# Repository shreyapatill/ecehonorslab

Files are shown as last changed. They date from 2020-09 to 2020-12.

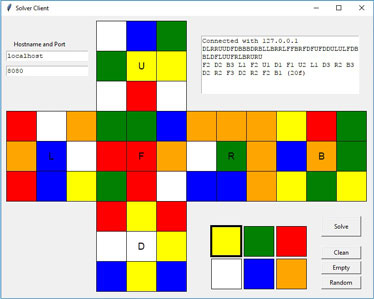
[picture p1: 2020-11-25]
RubiksSolver/gui_client.jpg

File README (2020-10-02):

By: Alex Zhang, Shreya Patil, Aryan Gupta
Project Proposal Guideline
Introduction

Statement of Purpose
The goal of our project is to construct and program a machine that can autonomously solve a Rubik’s Cube puzzle, starting from any random combination. 

Background Research

We are working on this project because we thought it would be cool to create something that could solve the complicated puzzle that is the Rubik’s Cube. We looked into what people have used to build a Rubik’s cube solver and modified their designs to build our project.
This project is similar to the Rubik’s Cube Solver back in Spring 2020. However, we plan to make the mechanical frame out of legos or 3d printing to cut down on cost and need for mechanical design experience. We also plan to use two cameras to scan the faces of the cube. 

System Overview

Rubik’s Cube: Would be a shame if this were missing...
UI: Where a human can input the colors of the faces. This is the input of the machine.
Each color has a number, you run a python code that allows you to type in the numbers that represent the cube
Data is sent to the Raspberry Pi by USB wire
IR Sensor: Senses whether the cube is in position and ready to be solved
Raspberry Pi: The brains. Figures out the status of the cube, calculates the solution, and sends the moves to the motors
Motor Drivers: The interface between the motor and the Pi
Stepper Motors: Rotates the faces of the cube to solve it

Parts

Rubik’s Cube
Rubik's Cube on Amazon
$6
Raspberry Pi 3 B+
ECE Supply Center - 740162520
$42
Raspberry Pi Power Supply
ECE Supply Center - 740162522
$11
MicroSD Card
MicroSD Card on Amazon 
$6
Six Stepper Motors
Stepper Motor
6 * 6 = $36 total
Holding torque: 0.26Nm (need 0.05Nm for speedcubes)
Set of Three Motor Drivers
Set of Three Motor Drivers on Amazon
$30
Mechanical Frame (3d printed or legos)
IR Sensors
IR Sensor on Amazon 
$9
TOTAL: $140 + legos (if we plan to go with those)
 
Possible Challenges

Frame design &  material (lego or 3-D printing?)
Creating a UI to input faces
Virtual communications/construction
Code it so the solver stops at the solution
 
References

	[1]J. Flatland and P. Rose, "jayflatland/HighFrequencyTwister", GitHub, 2020. [Online]. Available: https://github.com/jayflatland/HighFrequencyTwister/blob/master/LICENSE. [Accessed: 18- Sep- 2020].
	[2]"Adafruit's Raspberry Pi Lesson 10. Stepper Motors", Adafruit Learning System, 2020. [Online]. Available: https://learn.adafruit.com/adafruits-raspberry-pi-lesson-10-stepper-motors. [Accessed: 18- Sep- 2020].
	[3]N. Knopf and J. Swiezy, Web.mit.edu, 2020. [Online]. Available: http://web.mit.edu/6.111/www/f2017/projects/knopf_Project_Design_Presentation.pdf. [Accessed: 18- Sep- 2020].
	[4]"rubix cube transparent - Google Search", Google.com, 2020. [Online]. Available: https://www.google.com/search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. [Accessed: 18- Sep- 2020].
	[5]SenorJuan, “Torque on Conventional Cubes,” SpeedSolving Puzzles Community, 27-Jan-2020. [Online]. Available: https://www.speedsolving.com/threads/torque-on-conventional-cubes.76309/. [Accessed: 20-Sep-2020]. 
	[6]"MineLT/CubeSolver", GitHub, 2020. [Online]. Available: https://github.com/MineLT/CubeSolver. [Accessed: 27- Sep- 2020].

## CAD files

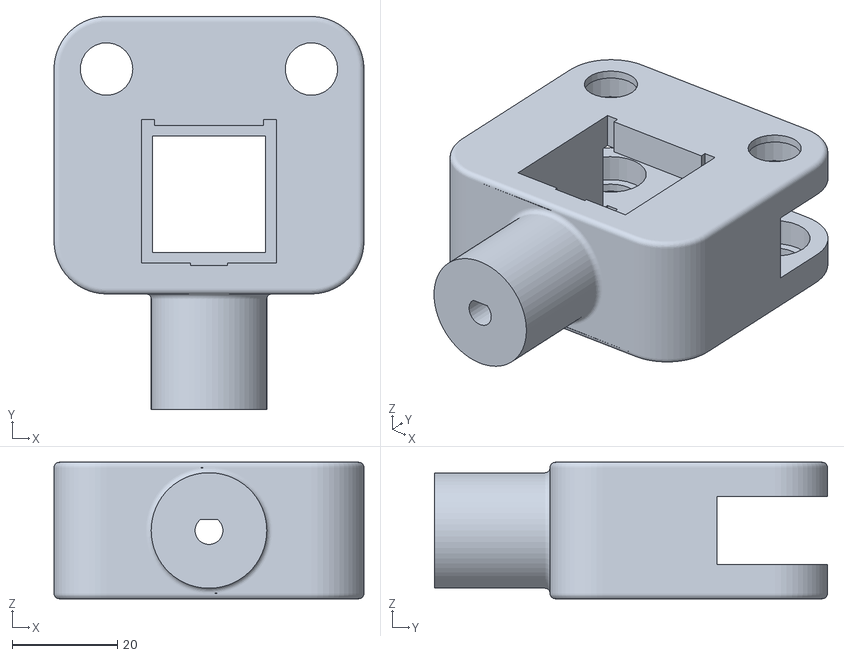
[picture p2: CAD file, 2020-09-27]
3d Models/Phase 5 Claw/Claw5 - Main Body.stl
59.0 x 74.8 x 26.0

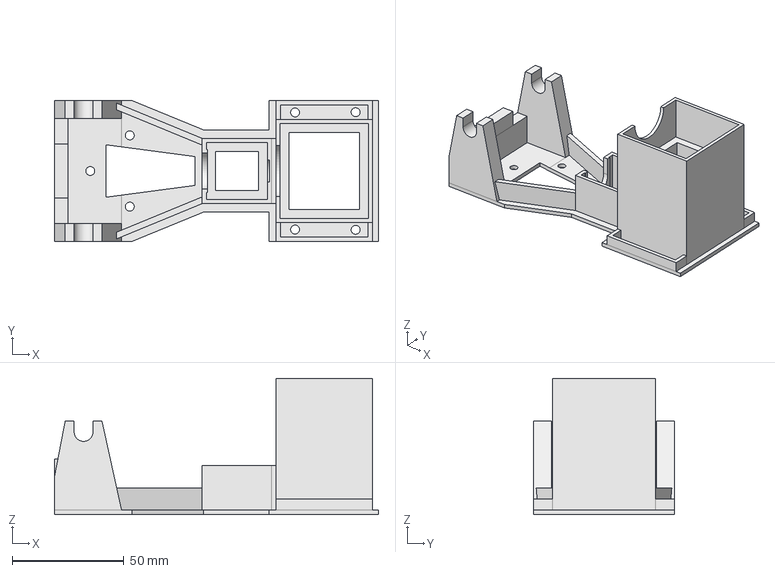
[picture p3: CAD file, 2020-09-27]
3d Models/Phase 2 Speedster/Assembly Tray.FCStd
144.9 x 63.0 x 61.0 mm

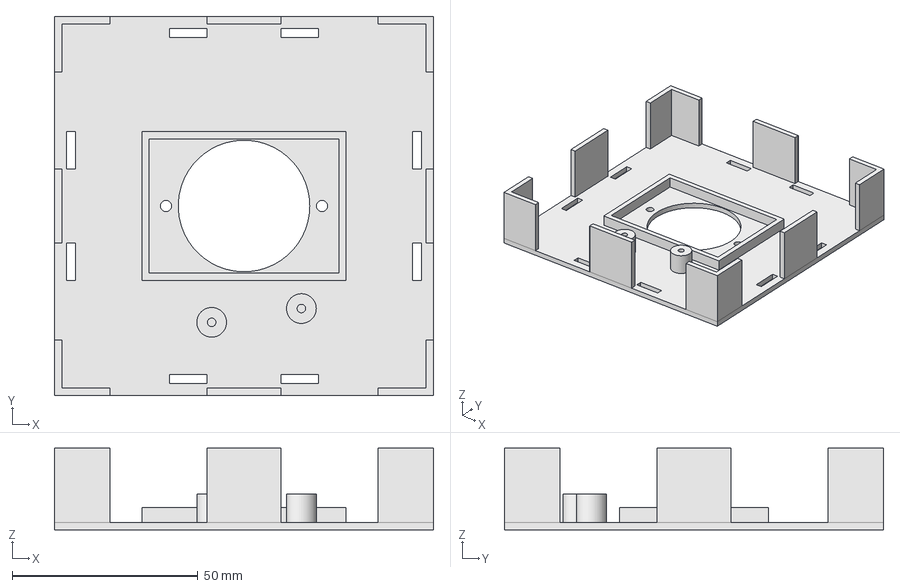
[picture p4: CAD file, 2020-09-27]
3d Models/Phase 1 Prototype/Rubiks Frame Bottom Top Small Steppers.FCStd
102.0 x 102.0 x 22.0 mm

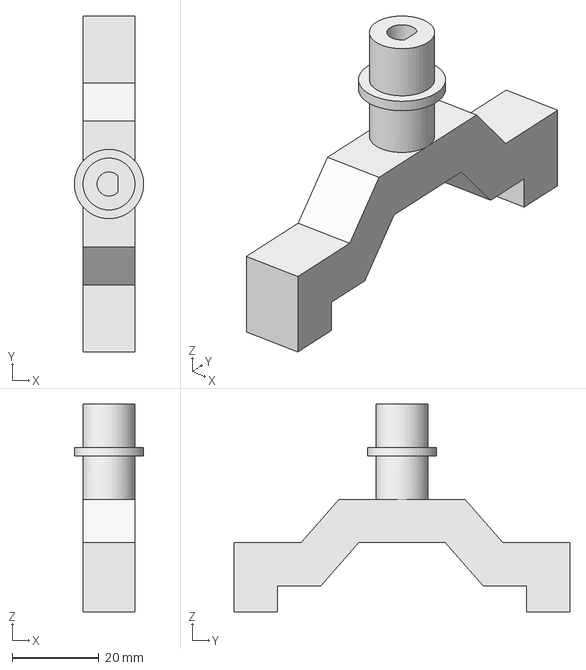
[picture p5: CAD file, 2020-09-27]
3d Models/Phase 2 Speedster/Fixed Claw.FCStd
16.0 x 77.5 x 48.0 mm

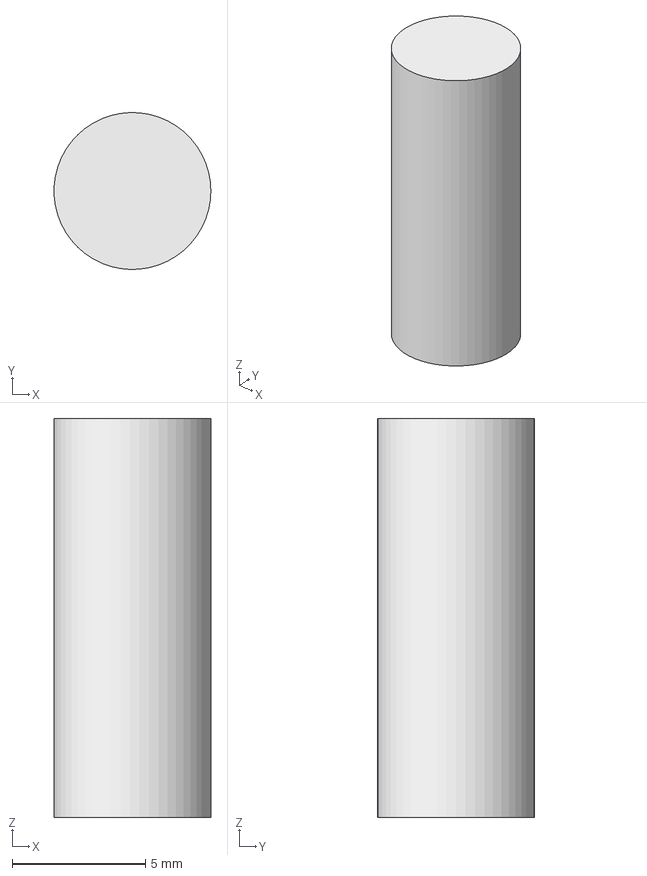
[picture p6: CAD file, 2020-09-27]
3d Models/Phase 3 Claw/Peg.FCStd
5.89 x 5.90 x 15.0 mm

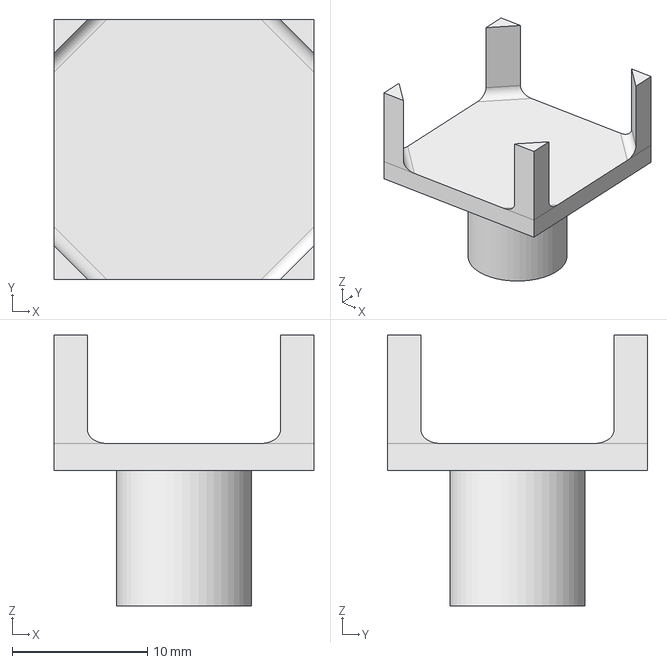
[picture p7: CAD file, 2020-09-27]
3d Models/Phase 4 Center Drive Redux/Center Drive Test 1.FCStd
19.2 x 19.2 x 20.0 mm

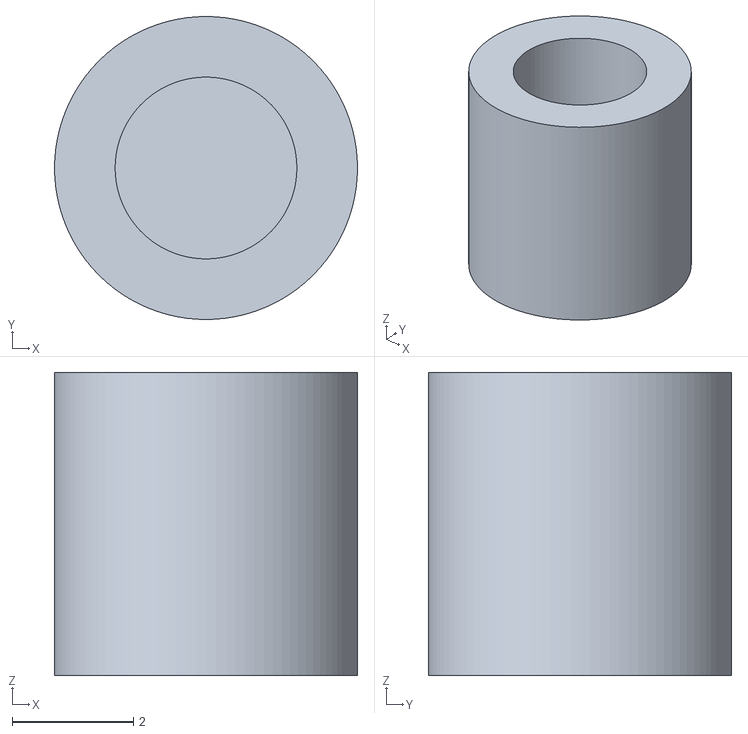
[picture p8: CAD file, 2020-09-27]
3d Models/Phase 1 Prototype/Small Stepper Drive Shaft Test Knob.STL
5.00 x 5.00 x 5.00

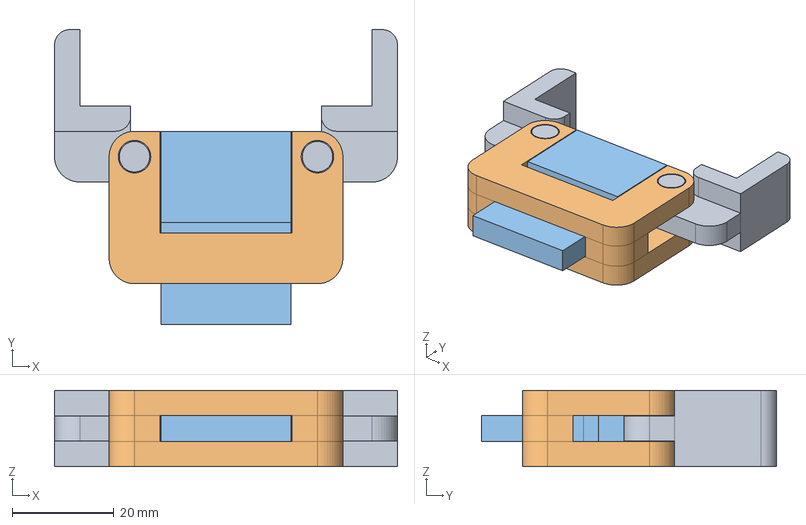
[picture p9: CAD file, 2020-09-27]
3d Models/Phase 3 Claw/Claw.FCStd
67.5 x 58.0 x 15.0 mm
Claws
Arms

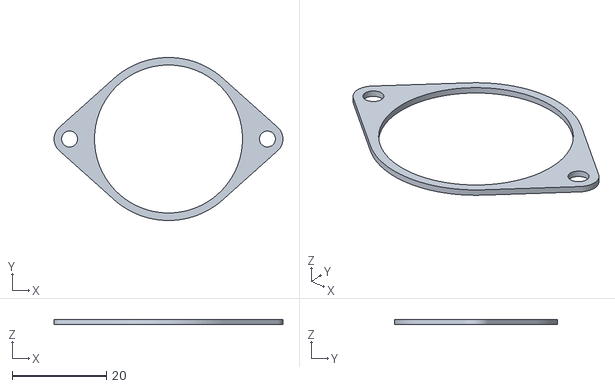
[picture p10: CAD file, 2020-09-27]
3d Models/Phase 1 Prototype/Small Stepper Bracket Template.STL
48.6 x 34.6 x 1.00

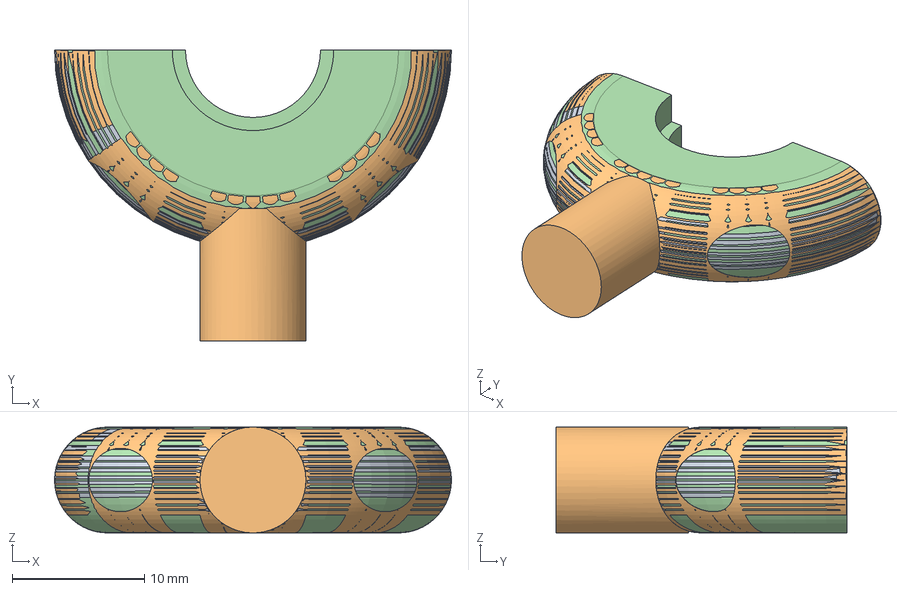
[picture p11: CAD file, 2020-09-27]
3d Models/Phase 2 Speedster/Push Ring.FCStd
30.0 x 22.0 x 8.00 mm
Top
Bottom

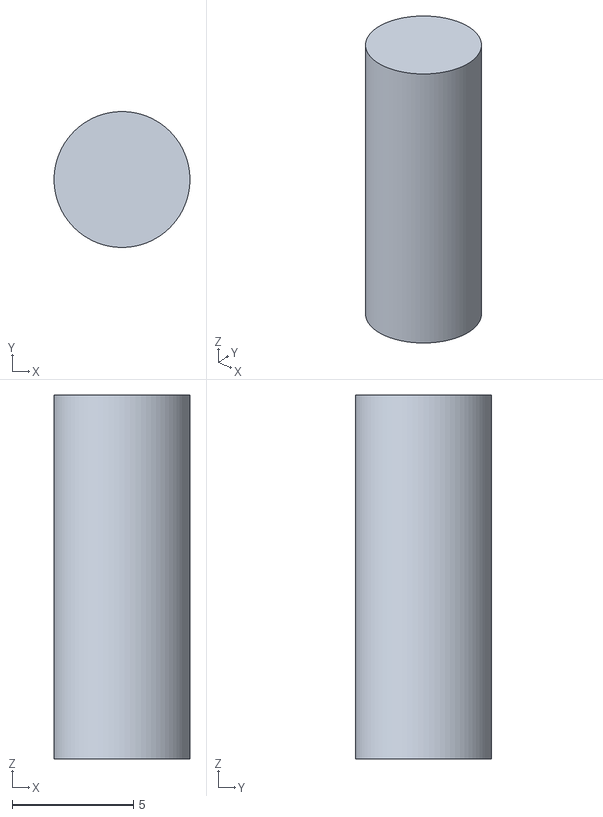
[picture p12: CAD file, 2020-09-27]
3d Models/Phase 3 Claw/Claw 2 - Peg.stl
5.60 x 5.60 x 15.0

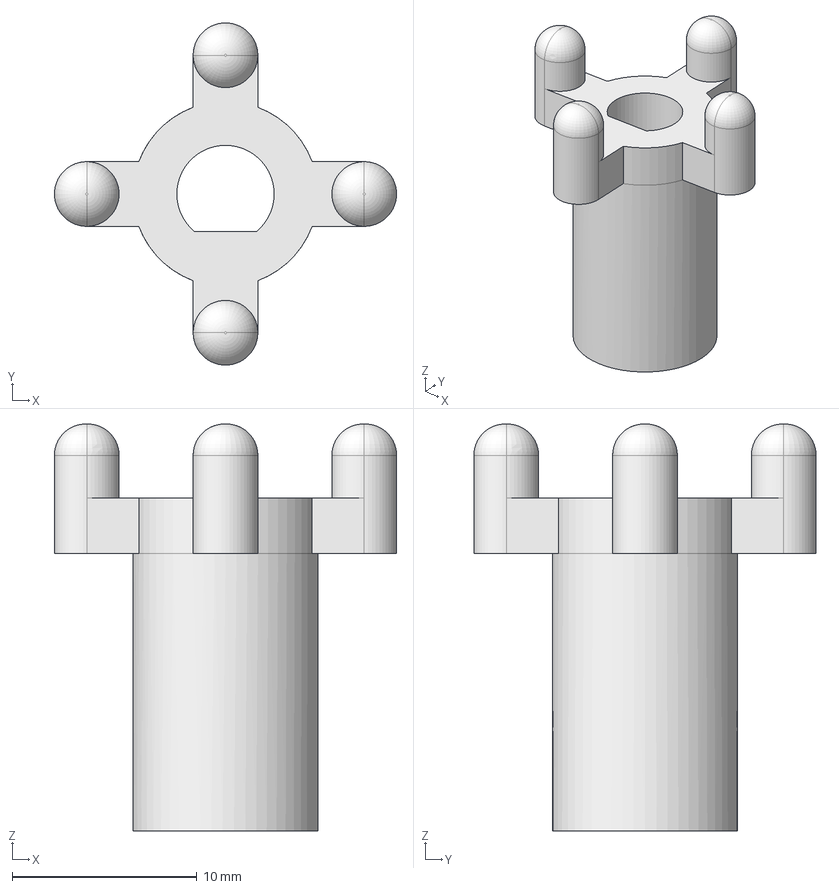
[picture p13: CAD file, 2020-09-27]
3d Models/Phase 4 Center Drive Redux/Drilled Cube Drive Bit.FCStd
18.5 x 18.5 x 22.0 mm

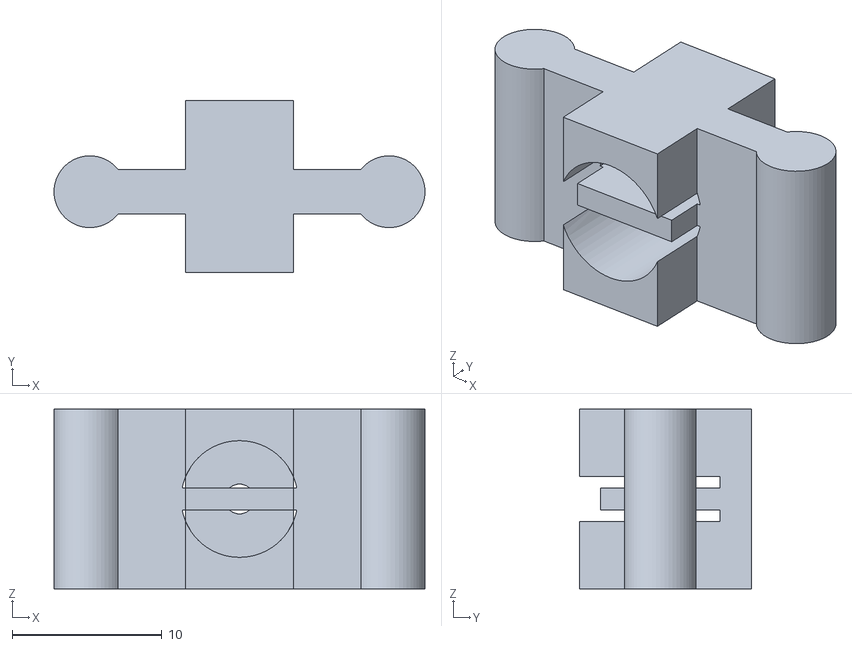
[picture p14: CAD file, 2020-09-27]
3d Models/Phase 5 Claw/Claw5 - Rocker.stl
24.8 x 11.5 x 12.0

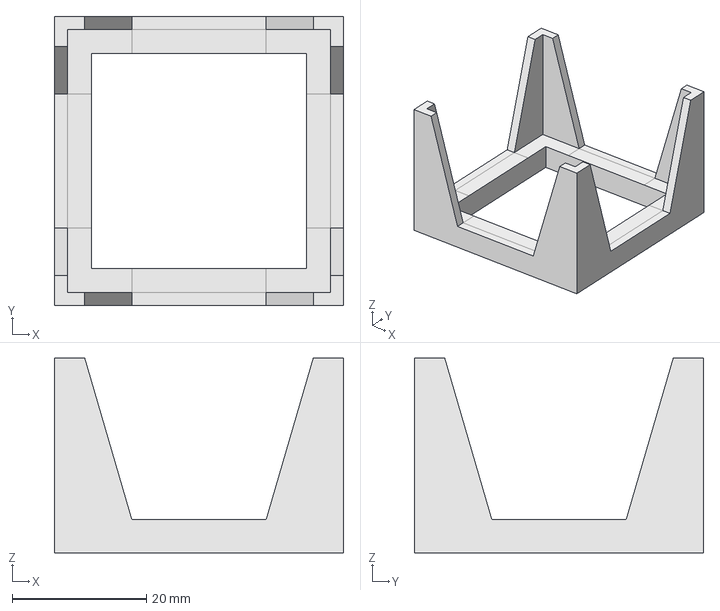
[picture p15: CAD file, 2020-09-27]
3d Models/Phase 1 Prototype/Rubiks Motor Bottom Bracket.FCStd
43.0 x 43.0 x 29.0 mm

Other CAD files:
3d Models/Phase 4 Center Drive Redux/Center Drive Test 2.FCStd
3d Models/Phase 5 Claw/Claw5.FCStd
3d Models/Phase 2 Speedster/Push Ring Bottom.stl
3d Models/Phase 3 Claw/Claw 2 - Feet.stl
3d Models/Phase 1 Prototype/Rubiks Center Square Foot 2 - Lego.stl
3d Models/Phase 1 Prototype/Rubiks Center Square Foot 2.FCStd
3d Models/Phase 1 Prototype/Rubiks Center Square Foot 2.stl
3d Models/Phase 1 Prototype/Rubiks Center Square Foot 3 - Capless Drive.FCStd
3d Models/Phase 1 Prototype/Rubiks Center Square Foot 3 - Capless Drive.stl
3d Models/Phase 1 Prototype/Rubiks Center Square Foot.FCStd
3d Models/Phase 1 Prototype/Rubiks Center Square Foot.stl
3d Models/Phase 1 Prototype/Rubiks Frame Bottom Top Small Steppers.stl
3d Models/Phase 1 Prototype/Rubiks Frame Fixed.ipt
3d Models/Phase 1 Prototype/Rubiks Frame Side Motor Shim.FCStd
3d Models/Phase 1 Prototype/Rubiks Frame Side Motor Shim.stl
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

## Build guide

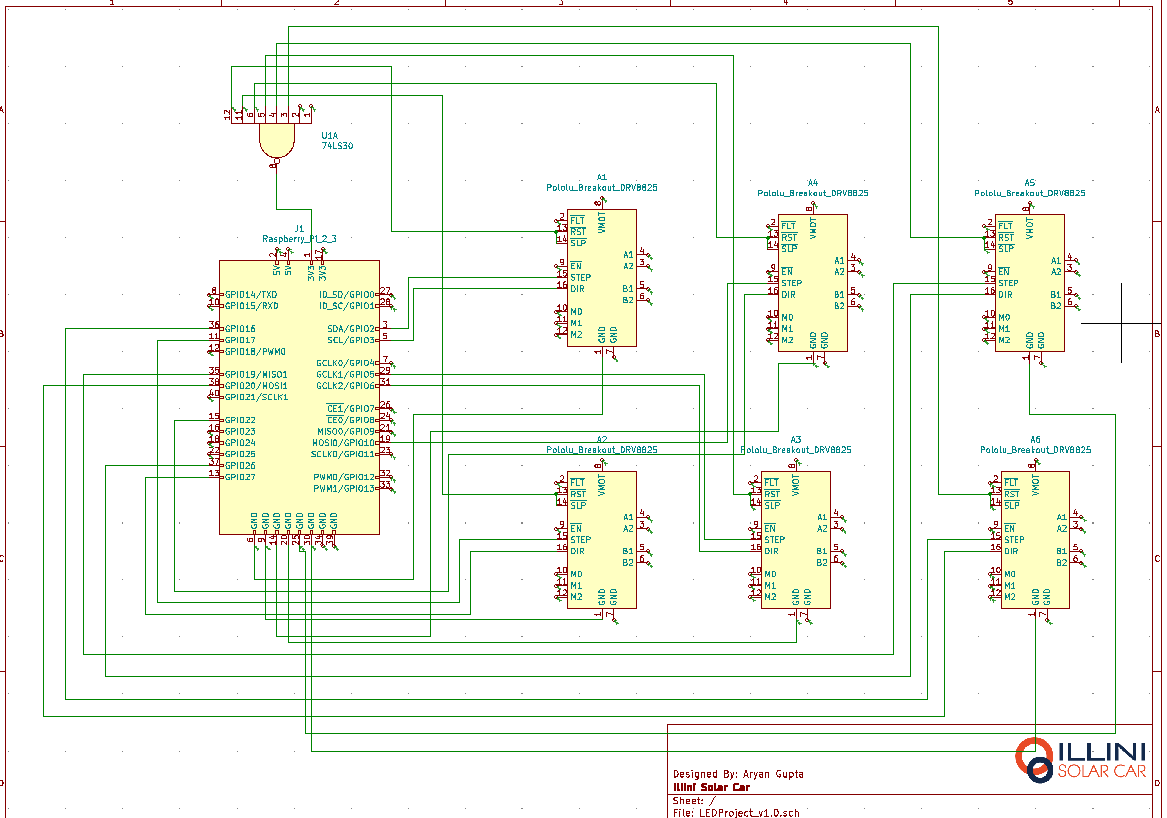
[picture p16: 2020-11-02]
schematics/wiring picture.png

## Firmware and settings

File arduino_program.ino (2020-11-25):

// motor control program, six stepper motors controlled from a python program.

// ############################################### ################################################# ##########
// Define the ports

// Definition A4998 F
# define  pinEnableF 30                                    // Activate A4998
# define  pinStepF    2                                    // Rising edge = one step.
# define  pinDirF     3                                    // Direction

// Definition A4998 R
# define  pinEnableR  34                                    // Activate A4998
# define  pinStepR    17                                    // Rising edge = one step.
# define  pinDirR     27                                    // Direction

// Definition A4998 B
# define  pinEnableB  38                                    // Activate A4998
# define  pinStepB    10                                    // Rising edge = one step.
# define  pinDirB     22                                    // Direction

// Definition A4998 L
# define  pinEnableL  42                                    // Activate A4998
# define  pinStepL     5                                    // Rising edge = one step.
# define  pinDirL      6                                    // Direction

// Definition A4998 D
# define  pinEnableD   46                                    // Activate A4998
# define  pinStepD     19                                    // Rising edge = one step.
# define  pinDirD      26                                    // Direction

// Definition A4998 U
# define  pinEnableU  50                                    // Activate A4998
# define  pinStepU    16                                    // Rising edge = one step.
# define  pinDirU     20                                    // Direction

# define  pinIRSensor 3                                     // Pin for IR Sensor

// ############################################### ################################################# ##########
// Declaration of the variables

# define  del  320                                          // Delay in microsecond between a rising sling and a falling sling
# define  acc  10                                           // Number of acceleration and deceleration steps to be performed with each movement
# define  vm   800                                          // Slowest speed at start of acceleration
# define  x (vm - del) / acc                                 // variable of acceleration functions

// ############################################### ################################################# ##########
// Table of movements

// All cases F, R, B, L, D, U, #, F ', R', B ', L', D ', U', #, F2, R2, B2, L2, D2, U2 , #, FB, FB ', FB2, F'B, F'B', F'B2, F2B, F2B ', F2B2, #, RL, RL', RL2, R'L, R'L ', R' L2, R2L, R2L ', R2L2, #, DU, DU', DU2, D'U, D'U ', D'U2, D2U, D2U', D2U2
// Order of the array F, R, B, L, D, U,
//                  F ', R', B ', L', D ', U',
//                  F2, R2, B2, L2, D2, U2,
//                  FB, FB ', F'B, F'B',
//                  F2B2, RL, RL ', R'L,
//                  R'L ', R2L2, DU, DU',
//                  D'U, D'U ', D2U2, FB2,
//                  F'B2, F2B, F2B ', RL2,
//                  R'L2, R2L, R2L ', DU2,
//                  D'U2, D2U, D2U '

int Tab [] [ 8 ] = {{ 1 , pinStepF, pinDirF, 0 , 50 }, { 1 , pinStepR, pinDirR, 0 , 50 }, { 1 , pinStepB, pinDirB, 0 , 50 }, { 1 , pinStepL, pinDirL, 0 , 50 }, { 1 , pinStepD, pinDirD, 0 , 50 }, { 1 , pinStepU, pinDirU, 0 , 50 },

               { 1 , pinStepF, pinDirF, 1 , 50 }, { 1 , pinStepR, pinDirR, 1 , 50 }, { 1 , pinStepB, pinDirB, 1 , 50 }, { 1 , pinStepL, pinDirL, 1 , 50 }, { 1 , pinStepD, pinDirD, 1 , 50 }, { 1 , pinStepU, pinDirU, 1 , 50 },
               
               { 1 , pinStepF, pinDirF, 0 , 100 }, { 1 , pinStepR, pinDirR, 0 , 100 }, { 1 , pinStepB, pinDirB, 0 , 100 }, { 1 , pinStepL, pinDirL, 0 , 100 }, { 1 , pinStepD, pinDirD, 0 , 100 }, { 1 , pinStepU, pinDirU, 0 , 100 },
               
               { 2 , pinStepF, pinStepB, pinDirF, pinDirB, 0 , 0 , 50 }, { 2 , pinStepF, pinStepB, pinDirF, pinDirB, 0 , 1 , 50 }, { 2 , pinStepF, pinStepB, pinDirF, pinDirB, 1 , 0 , 50 }, { 2 , pinStepF, pinStepB, pinDirF, pinDirB, 1 , 1 , 50 },

               { 2 , pinStepF, pinStepB, pinDirF, pinDirB, 0 , 0 , 100 }, { 2 , pinStepR, pinStepL, pinDirR, pinDirL, 0 , 0 , 50 }, { 2 , pinStepR, pinStepL, pinDirR, pinDirL, 0 , 1 , 50 }, { 2 , pinStepR, pinStepL, pinDirR, pinDirL, 1 , 0 , 50 },
               
               { 2 , pinStepR, pinStepL, pinDirR, pinDirL, 1 , 1 , 50 }, { 2 , pinStepR, pinStepL, pinDirR, pinDirL, 0 , 0 , 100 }, { 2 , pinStepD, pinStepU, pinDirD, pinDirU, 0 , 0 , 50 }, { 2 , pinStepD, pinStepU, pinDirD, pinDirU, 0 , 1 , 50 },
               
               { 2 , pinStepD, pinStepU, pinDirD, pinDirU, 1 , 0 , 50 }, { 2 , pinStepD, pinStepU, pinDirD, pinDirU, 1 , 1 , 50 }, { 2 , pinStepD, pinStepU, pinDirD, pinDirU, 0 , 0 , 100 }, { 3 , pinStepF, pinStepB, pinDirF, pinDirB, 0 },

               { 3 , pinStepF, pinStepB, pinDirF, pinDirB, 1 }, { 3 , pinStepB, pinStepF, pinDirB, pinDirF, 0 }, { 3 , pinStepB, pinStepF, pinDirB, pinDirF, 1 }, { 3 , pinStepR, pinDirte , pinDirL, 0 },

               { 3 , pinStepR, pinStepL, pinDirR, pinDirL, 1 }, { 3 , pinStepL, pinStepR, pinDirL, pinDirR, 0 }, { 3 , pinStepL, pinStepR, pinDirL, pinDirR, 1 }, { 3 , pinStepD, pinDirtep , pinDirU, 0 },
               
               { 3 , pinStepD, pinStepU, pinDirD, pinDirU, 1 }, { 3 , pinStepU, pinStepD, pinDirU, pinDirD, 0 }, { 3 , pinStepU, pinStepD, pinDirU, pinDirD, 1 }};

// ############################################### ################################################# ##########
// Setup

void  setup () {

Serial. begin ( 9600 );
Serial. println ( " Engine Program " );

// Setup control port (5V)
pinMode (pinEnableF, OUTPUT);
pinMode (pinDirF, OUTPUT);
pinMode (pinStepF, OUTPUT);

// Setup control port (5V)
pinMode (pinEnableR, OUTPUT);
pinMode (pinDirR, OUTPUT);
pinMode (pinStepR, OUTPUT);

// Setup control port (5V)
pinMode (pinEnableB, OUTPUT);
pinMode (pinDirB, OUTPUT);
pinMode (pinStepB, OUTPUT);

// Setup control port (5V)
pinMode (pinEnableL, OUTPUT);
pinMode (pinDirL, OUTPUT);
pinMode (pinStepL, OUTPUT);

// Setup control port (5V)
pinMode (pinEnableD, OUTPUT);
pinMode (pinDirD, OUTPUT);
pinMode (pinStepD, OUTPUT);

// Setup control port (5V)
pinMode (pinEnableU, OUTPUT);
pinMode (pinDirU, OUTPUT);
pinMode (pinStepU, OUTPUT);

// Setup IR sensor
pinMode (pinIRSensor, INPUT)

// Setup of the "pinEnable" ports (blocking of the motor axes)
digitalWrite (pinEnableF, LOW);
digitalWrite (pinEnableR, LOW);
digitalWrite (pinEnableB, LOW);
digitalWrite (pinEnableL, LOW);
digitalWrite (pinEnableD, LOW);
digitalWrite (pinEnableU, LOW);
}
// ############################################### ################################################# ##########
// Movement control method

//
// Only one face turns (regardless of the direction and the direction)
//
void  OneSideMvt ( int pinStep, int pinDir, bool dir, int nbrPas) {
digitalWrite (pinDir, dir);                              // choice of direction
for ( int i = 0 ; i <acc; i ++) {                           // only one face turns
   digitalWrite (pinStep, HIGH);                         // The motor advances by one step (rising edge)
   delayMicroseconds (vm - i * x);
   digitalWrite (pinStep, LOW);                          // falling edge
   delayMicroseconds (vm - i * x);
  }
for ( int i = 0 ; i <nbrPas - 2 * acc; i ++) {                // only one face turns
   digitalWrite (pinStep, HIGH);                         // The motor advances by one step (rising edge)
   delayMicroseconds (del);
   digitalWrite (pinStep, LOW);                          // falling edge
   delayMicroseconds (del);
  }
for ( int i = 0 ; i <acc; i ++) {                           // only one face turns
   digitalWrite (pinStep, HIGH);                         // The motor advances by one step (rising edge)
   delayMicroseconds (del + i * x);
   digitalWrite (pinStep, LOW);                          // falling edge
   delayMicroseconds (del + i * x);
  }
}

//
// Both faces take the same number of steps (regardless of the direction and the direction)
//
void  TwoSidesSameMvt ( int pinStep1, int pinStep2, int pinDir1, int pinDir2, bool dir1, bool dir2, int nbrPas) {
digitalWrite (pinDir1, dir1);
digitalWrite (pinDir2, dir2);
for ( int i = 0 ; i <acc; i ++) {                           // Both faces turn
   digitalWrite (pinStep1, HIGH);                        // Motor1 advances by one step (rising edge)
   digitalWrite (pinStep2, HIGH);                        // Motor2 advances by one step (rising edge)
   delayMicroseconds (vm - i * x);
   digitalWrite (pinStep1, LOW);                         // falling edge
   digitalWrite (pinStep2, LOW);                         // falling edge
   delayMicroseconds (vm - i * x);
  }
for ( int i = 0 ; i <nbrPas - 2 * acc; i ++) {                // Both faces turn
   digitalWrite (pinStep1, HIGH);                        // Motor1 advances by one step (rising edge)
   digitalWrite (pinStep2, HIGH);                        // Motor2 advances by one step (rising edge)
   delayMicroseconds (del);
   digitalWrite (pinStep1, LOW);                         // falling edge
   digitalWrite (pinStep2, LOW);                         // falling edge
   delayMicroseconds (del);
  }
for ( int i = 0 ; i <acc; i ++) {                           // Both faces turn
   digitalWrite (pinStep1, HIGH);                        // Motor1 advances by one step (rising edge)
   digitalWrite (pinStep2, HIGH);                        // Motor2 advances by one step (rising edge)
   delayMicroseconds (del + i * x);
   digitalWrite (pinStep1, LOW);                         // falling edge
   digitalWrite (pinStep2, LOW);                         // falling edge
   delayMicroseconds (del + i * x);
  }
}

//
// one of the two faces is 50 steps, the other is 100 (regardless of the direction and the direction)
//
void  TwoSidesNotSameMvt ( int pinStep1, int pinStep2, int pinDir1, int pinDir2, bool dir1) {
int nbrPas = 50 ;
digitalWrite (pinDir1, dir1);
digitalWrite (pinDir2, dir1);
for ( int i = 0 ; i <acc; i ++) {                           // Both faces turn
   digitalWrite (pinStep1, HIGH);                        // Motor1 advances by one step (rising edge)
   digitalWrite (pinStep2, HIGH);                        // Motor2 advances by one step (rising edge)
   delayMicroseconds (vm - i * x);
   digitalWrite (pinStep1, LOW);                         // falling edge
   digitalWrite (pinStep2, LOW);                         // falling edge
   delayMicroseconds (vm - i * x);
   digitalWrite (pinStep2, HIGH);                        // Motor2 advances by one step (rising edge)
   delayMicroseconds (vm - i * x);
   digitalWrite (pinStep2, LOW);                         // falling edge
   delayMicroseconds (vm - i * x);
  }
for ( int i = 0 ; i <nbrPas - 2 * acc; i ++) {                // Both faces turn
   digitalWrite (pinStep1, HIGH);                        // Motor1 advances by one step (rising edge)
   digitalWrite (pinStep2, HIGH);                        // Motor2 advances by one step (rising edge)
   delayMicroseconds (del);
   digitalWrite (pinStep1, LOW);                         // falling edge
   digitalWrite (pinStep2, LOW);                         // falling edge
   delayMicroseconds (del);
   digitalWrite (pinStep2, HIGH);                        // Motor2 advances by one step (rising edge)
   delayMicroseconds (del);
   digitalWrite (pinStep2, LOW);                         // falling edge
   delayMicroseconds (del);
  }
for ( int i = 0 ; i <acc; i ++) {                           // Both faces turn
   digitalWrite (pinStep1, HIGH);                        // Motor1 advances by one step (rising edge)
   digitalWrite (pinStep2, HIGH);                        // Motor2 advances by one step (rising edge)
   delayMicroseconds (del + i * x);
   digitalWrite (pinStep1, LOW);                         // falling edge
   digitalWrite (pinStep2, LOW);                         // falling edge
   delayMicroseconds (del + i * x);
   digitalWrite (pinStep2, HIGH);                        // Motor2 advances by one step (rising edge)
   delayMicroseconds (del + i * x);
   digitalWrite (pinStep2, LOW);                         // falling edge
   delayMicroseconds (del + i * x);
  }
}

// ############################################### ################################################# ##########

void  loop () {
int statusSensor = digitalRead (pinIRSensor);

if (statusSensor == 1) {
  if (Serial. available ()) {
    int r = Serial. read () - 65 ;                           // r: index of the movement in the Tab array
    if (Tab [r] [ 0 ] == 1 ) {                                  // call the OneSideMvt method
      OneSideMvt (Tab [r] [ 1 ], Tab [r] [ 2 ], Tab [r] [ 3 ], Tab [r] [ 4 ]);
      Serial. print (r);
      }
    else  if (Tab [r] [ 0 ] == 2 ) {                             // call the TwoSidesSameMvt method
      TwoSidesSameMvt (Tab [r] [ 1 ], Tab [r] [ 2 ], Tab [r] [ 3 ], Tab [r] [ 4 ], Tab [r] [ 5 ], Tab [r] [ 6 ], Tab [r] [ 7 ]);
      }
    else  if (Tab [r] [ 0 ] == 3 ) {                             // call the TwoSidesNotSameMvt method
      TwoSidesNotSameMvt (Tab [r] [ 1 ], Tab [r] [ 2 ], Tab [r] [ 3 ], Tab [r] [ 4 ], Tab [r] [ 5 ]);
      }
    }
  }
}

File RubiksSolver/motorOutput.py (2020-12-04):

import RPi.GPIO as GPIO
import time

#define some constants
CW = 1
CCW = 0
SPR = 50 #value found by testing
step_count = SPR
delay = 0.0058 #speeeed

def motorSolve(solveString):
    #input: a string of the moves to perform
    #parses string and executes the moves

    GPIO.setmode(GPIO.BCM)

    #sets up all the pins
    stepF = 2
    dirF = 3
    GPIO.setup(stepF, GPIO.OUT)
    GPIO.setup(dirF, GPIO.OUT)

    stepR = 17
    dirR = 27
    GPIO.setup(stepR, GPIO.OUT)
    GPIO.setup(dirR, GPIO.OUT)

    stepB = 10
    dirB = 22
    GPIO.setup(stepB, GPIO.OUT)
    GPIO.setup(dirB, GPIO.OUT)

    stepL = 5
    dirL = 6
    GPIO.setup(stepL, GPIO.OUT)
    GPIO.setup(dirL, GPIO.OUT)

    stepD = 19
    dirD = 26
    GPIO.setup(stepD, GPIO.OUT)
    GPIO.setup(dirD, GPIO.OUT)

    stepU = 16
    dirU = 20
    GPIO.setup(stepU, GPIO.OUT)
    GPIO.setup(dirU, GPIO.OUT)

    #parse input
    toSolve = solveString.split()
    toSolve = toSolve[:-1] #the last one is how many moves there are, we don't need it
    #print("SOLVING: ", end = '')
    #print(toSolve)

    #moves
    for move in toSolve: #move format: F1, F is face to move, 1 is how many 90 degree turns to make
        #print(move)
        step_count = 50
        #step counts are hard coded because sometimes the faces act weird and must be calibrated individually
        #clock also hard coded because in the future we can change it easier
        if move[0] == "F":
            step = stepF
            direc = dirF
            clock = CCW
            step_count = 50
        if move[0] == "U":
            step = stepU
            direc = dirU
            clock = CCW
            step_count = 50
        if move[0] == "B":
            step = stepB
            direc = dirB
            clock = CCW
            step_count = 50
        if move[0] == "R":
            step = stepR
            direc = dirR
            clock = CCW
            step_count = 50
        if move[0] == "L":
            step = stepL
            direc = dirL
            clock = CCW
            step_count = 50
        if move[0] == "D":
            step = stepD
            direc = dirD
            clock = CCW
            step_count = 50
        
        #if we're turning 3 times, just turn once the opposite direction
        toTurn = int(move[1])
        if int(move[1]) == 3:
            toTurn = 1
            if clock == CCW:
                clock = CW
            else:
                clock = CCW
        
        #perform move
        for i in range(toTurn):
            GPIO.output(direc, clock)
            #spins the motor 90 degrees
            for j in range(step_count):
                GPIO.ouput(step, GPIO.HIGH)
                time.sleep(delay)
                GPIO.output(step, GPIO.LOW)
                time.sleep(delay)

GPIO.cleanup()

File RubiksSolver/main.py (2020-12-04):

from tkinter import *
import solver as sv
import motorOutput
import sensor_led_output
import time

root = Tk()

# creating a Label widget (directions)
directions = Label(root,
                   text="Click on tile to change color. Be sure to match your inputs exactly to the pattern on your Rubik's Cube.").grid(
    row=0, columnspan=12)

# initial color input
# U=blue, L=orange, F=white, R=red, B=yellow, D=green
colors = ["U", "U", "U",
          "U", "U", "U",
          "U", "U", "U",
          "L", "L", "L", "F", "F", "F", "R", "R", "R", "B", "B", "B",
          "L", "L", "L", "F", "F", "F", "R", "R", "R", "B", "B", "B",
          "L", "L", "L", "F", "F", "F", "R", "R", "R", "B", "B", "B",
          "D", "D", "D",
          "D", "D", "D",
          "D", "D", "D"]
# array of buttons to represent tiles
tiles = []

# changes color of tiles on click
def color_change(i, bt):
    if colors[i] == "U":
        bt.configure(bg="yellow")
        colors[i] = "B"
    elif colors[i] == "B":
        bt.configure(bg="white")
        colors[i] = "F"
    elif colors[i] == "F":
        bt.configure(bg="orange")
        colors[i] = "L"
    elif colors[i] == "L":
        bt.configure(bg="green")
        colors[i] = "D"
    elif colors[i] == "D":
        bt.configure(bg="red")
        colors[i] = "R"
    elif colors[i] == "R":
        bt.configure(bg="blue")
        colors[i] = "U"

# creates top face
for tile_number in range(0, 9):
    temp_button = Button(root, text=str(tile_number), height=3, width=6, bg="blue")

    if tile_number != 4:  # all but center tile can change color
        temp_button.configure(command=lambda i=tile_number, j=temp_button: color_change(i, j))

    col = tile_number % 3 + 3
    ro = int(tile_number / 3) + 6
    temp_button.grid(row=ro, column=col)
    tiles.append(temp_button)

# creates middle faces
for tile_number in range(9, 45):
    temp_button = Button(root, text=str(tile_number), height=3, width=6)

    if colors[tile_number] == "L":
        temp_button.configure(bg="orange")
    elif colors[tile_number] == "F":
        temp_button.configure(bg="white")
    elif colors[tile_number] == "R":
        temp_button.configure(bg="red")
    else:
        temp_button.configure(bg="yellow")

    if tile_number != 22 and tile_number != 25 and tile_number != 28 and tile_number != 31:
        temp_button.configure(command=lambda i=tile_number, j=temp_button: color_change(i, j))

    col = (tile_number + 3) % 12
    ro = int((tile_number + 3) / 12) + 8
    temp_button.grid(row=ro, column=col)
    tiles.append(temp_button)

# creates bottom face
for tile_number in range(45, 54):
    temp_button = Button(root, text=str(tile_number), height=3, width=6, bg="green")

    if tile_number != 49:  # all but center tile can change color
        temp_button.configure(command=lambda i=tile_number, j=temp_button: color_change(i, j))

    col = tile_number % 3 + 3
    ro = int(tile_number / 3) + 12
    temp_button.grid(row=ro, column=col)
    tiles.append(temp_button)


# method to print the tile colors
def print_colors():
    color_input = Label(root, text=colors).grid(row=2, columnspan=12)
    return colors

# submit button that returns the array of colors
color_button = Button(root, text="Print colors", command=print_colors).grid(row=1, columnspan=12)


# method to check number of tiles for each color
def check_tiles():
    count_dict = {i: colors.count(i) for i in colors}
    count_print = Label(root, text=count_dict).grid(row=4, columnspan=12)
    for key in count_dict:
        if (count_dict[key] > 9):
            invalid = Label(root, text="Invalid input", bg='red').grid(row=5, columnspan=12)
            break
    else:
        valid = Label(root,text="   Valid input   ").grid(row=5, columnspan=12) #extra whitespace so red from invalid doesn't show up


#cubestring = 'DUUBULDBFRBFRRULLLBRDFFFBLURDBFDFDRFRULBLUFDURRBLBDUDL'  # cube definition string of cube we want to solve
# See module enums.py for the format of the cube definition string

#Orignal cubestring, must convert
#               ----------------
#               | 0  | 1  | 2  |
#               ----------------
#               | 3  | 4  | 5  |
#               ----------------
#               | 6  | 7  | 8  |
#               ----------------
#-------------------------------------------------------------
#| 9  | 10 | 11 | 12 | 13 | 14 | 15 | 16 | 17 | 18 | 19 | 20 |
#-------------------------------------------------------------
#| 21 | 22 | 23 | 24 | 25 | 26 | 27 | 28 | 29 | 30 | 31 | 32 |
#-------------------------------------------------------------
#| 33 | 34 | 35 | 36 | 37 | 38 | 39 | 40 | 41 | 42 | 43 | 44 |
#-------------------------------------------------------------
#               ----------------
#               | 45 | 46 | 47 |
#               ----------------
#               | 48 | 49 | 50 |
#               ----------------
#               | 51 | 52 | 53 |
#

def converter(cubeArray):
    #input: an array with cube letters in above format
    #output: a string with cube letters in below format
    toReturn = ""
    for i in range(9): #U face
        toReturn += cubeArray[i]
    toReturn += cubeArray[15] + cubeArray[16] + cubeArray[17] #R face
    toReturn += cubeArray[27] + cubeArray[28] + cubeArray[29]
    toReturn += cubeArray[39] + cubeArray[40] + cubeArray[41]
    toReturn += cubeArray[12] + cubeArray[13] + cubeArray[14] #F face
    toReturn += cubeArray[24] + cubeArray[25] + cubeArray[26]
    toReturn += cubeArray[36] + cubeArray[37] + cubeArray[38]
    for i in range(45, 54): #D face
        toReturn += cubeArray[i]
    toReturn += cubeArray[9]  + cubeArray[10] + cubeArray[11] #L face
    toReturn += cubeArray[21] + cubeArray[22] + cubeArray[23]
    toReturn += cubeArray[33] + cubeArray[34] + cubeArray[35]
    toReturn += cubeArray[18] + cubeArray[19] + cubeArray[20] #B face
    toReturn += cubeArray[30] + cubeArray[31] + cubeArray[32]
    toReturn += cubeArray[42] + cubeArray[43] + cubeArray[44]
    return toReturn
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

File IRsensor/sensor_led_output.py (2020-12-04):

import RPi.GPIO as GPIO
import time

sensor = 21  # GPIO pin number
led = 18
button = 15

GPIO.setmode(GPIO.BOARD)
GPIO.setup(sensor, GPIO.IN)
GPIO.setup(button, GPIO.IN)
GPIO.setup(led, GPIO.OUT)

GPIO.output(led, False)
print("IR Sensor Ready.....")
print(" ")

try:
    while True:
        if GPIO.input(sensor) and GPIO.input(button):  # checks if both sensor sees something and button is pushed
            GPIO.output(led, True)
            print("Object Detected")
            while GPIO.input(sensor) and GPIO.input(button):
                time.sleep(0.2)
        else:
            GPIO.output(led, False)


except KeyboardInterrupt:
    GPIO.cleanup()

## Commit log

2020-09-27 moved Phase folders to 3D Model folder
    [Assembly Tray.FCStd, Assembly Tray.stl, Base Plate.FCStd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]
2020-10-10 Fixed import errors and bugs in cobeSolver
    [main.py]
2020-11-02 Create arduino problem.ino
    Copy pasted from https://github.com/MineLT/CubeSolver/blob/master/arduino%20program.ino
    [arduino program.ino]
2020-11-02 Update arduino program.ino
2020-11-07 Update arduino program.ino
    fixed incorrect comments
    [arduino program.ino]
2020-11-12 IR Sensor code
2020-11-23 Fix pin number for face U's direction
    [arduino_program.ino]
2020-11-25 Updated pin numbers
2020-11-25 Solver is called on correct cube now
    [main.py]
2020-11-26 Motor movement
